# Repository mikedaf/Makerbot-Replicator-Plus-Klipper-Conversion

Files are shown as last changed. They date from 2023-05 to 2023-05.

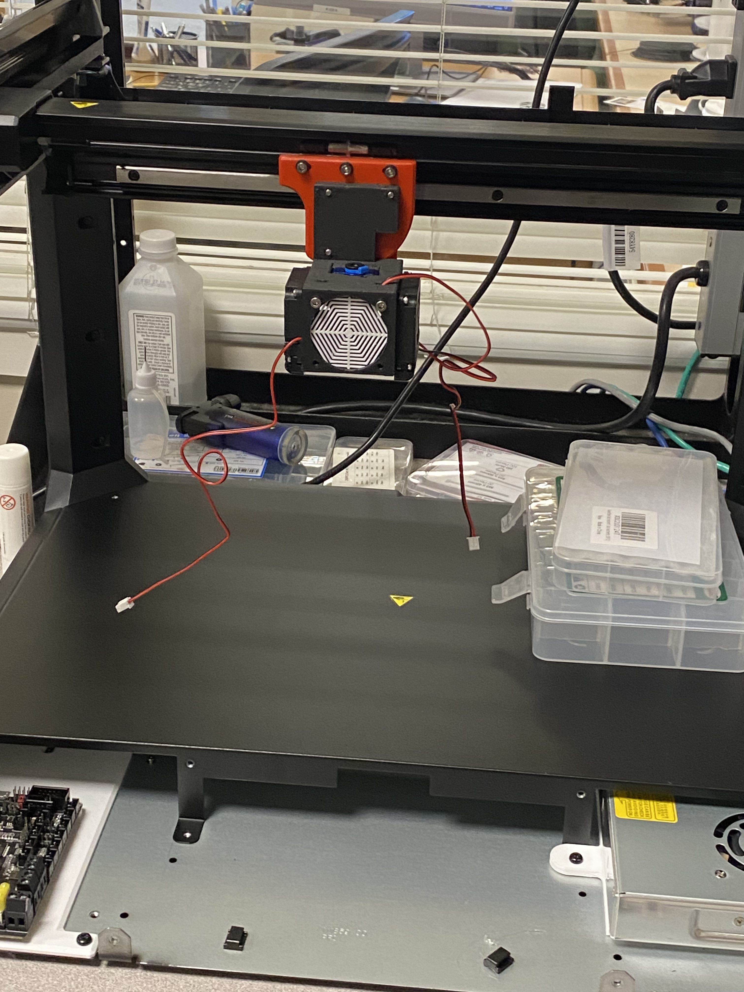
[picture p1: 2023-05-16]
Build Images/IMG_1790.jpg

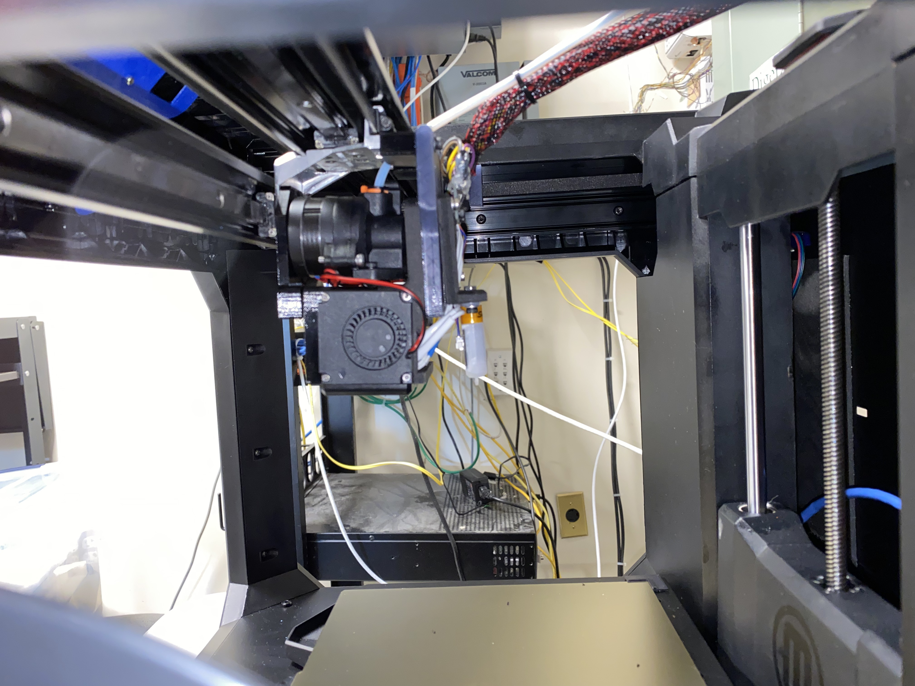
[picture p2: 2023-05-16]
Build Images/IMG_2500.jpg

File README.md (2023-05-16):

Here is everything I used to convert our Makerbot Replicator to a fairly capable klipper machine with a heated bed and input shaper.

I heavily used Rolohaun's makerbot replicator 5th gen parts for this, but I had to change some things for this specific printer. https://github.com/rolohaun/Replicator5-Klipper

This build uses M3 M2.5 and M2 screws, I used socket head ones, but any should be fine. Just be careful not to split the parts if you use countersunk screws. You'll need to source a good amount of M3 screws from M3x6 to M3x50. a regular M2.5 and M2 kit should cover those fine.

Some items may not work as intended, I've never done this before so let me know if something isn't working. The screen mount will probably not work as it is at the moment, but some post processing got it there for me.

I've included my toolhead STEP file, hopefully it can prove useful if anyone needs to make any changes.

I will comment out everything from the configs that won't run on an initial klipper setup, so make sure to uncomment these as you install ADXL support and so on.

I mounted the raspberry pi to where the old screen PCB and other bits were located. Use the original face plate piece and just replace the metal bracket with the printed one. You may have to cut some holes into the face plate sides to achieve enough room for the pi. I couldn't fit a power plug in there, so I soldered a ground wire to the usb housing chasis and stuck power across the two front GPIO pinsto save space. I hotglued the original encoder wheel back in place, but this is completely optional. The several usb,ethernet, and ADXL wires can be run along the top of the motion system where the original HMDI cord was set, there is enough room where they don't get pinched, but be careful because it's very easy for a wire to move into a location where it will get pinched. (Make sure to wire the original ground from the motion system frame into a common ground(also a good idea to do this with the PSU body))

The SKR Mini e3 v3 and Meanwell 350 PSU go in fairly simple, you'll need to have the entire machine apart for this, but you should already be there from taking the old parts out. Run the mainboard power wires around the same way the stock ones were run (under and in front of the Z platform). I cut a hole in the back panel and wired up a standard plug socket as well as an ethernet wall port and a plug for the Rpi power. this isn't difficult as theres plenty of room, but it can be a pain to get through that thick metal unless you have sufficient tools. The mainboard mount and the mainboard fan mount will sandwich the SKR mini together, but it can be easier to install the board on the mounting plate first with 1 or 2 of the thumbscrews, and then put the fans on with screws from the bottom. Make sure to only put the thumbscrews on the mounting point NOT used by the fan mounts.

The toolhead is a bit complex, it's probably easiest to assemble most of it outside the printer with the mainboard side wires disconnected. Use the dragonfly spacer and screw down the hotend (pretty much everything should use threaded inserts here). Now you can use the 4010 blower fans to hold the back and front hotend halves together (don't put any screws in the front top holes for the fan yet). Now is a good time to put the inserts for the LDO orbiter in place, and screw that down (the PTFE tube can be tricky to cut to length). Now screw the Toolhead mounting plate with 3 M3 screws along with the bltouch bracket to the back of the hotend assembly (the cables should be able to route through this part) You can then put the 4010 axial fan into the Front hotend part along with the fan grill and route the cable through one of the top holes (you'll need to cut the connector off if it has one).Next you'll go over to the metal plate that attaches the two rail carriages together on the printer, and just take out the 4 screws on the bottom vertical part. Then you'll mount the "Rail-Fan Mount" and screw that down. Then stick two M3x45-50 screws into the front two holes of that, followed by 3 washers on each one after they're pushed in. Now you can take the toolhead assembly and push it over the two long screws coming from the rail mount and it should hold everything in place. Don't full tighten this down yet, but instead put the Toolhead mounting spacer in place where it will screw into the original toolhead mounting holes (3 M3 holes). Now tighten everything in place and the toolhead should be good.

The cable guide just VHB tapes to the open rectangle shaped hole towards the back of the machine, this is covering the spot where the old spool holder was. That is completely useless to us now, so we'll cover it up with this. This can be added or removed after the hotend is already wired and tied up.

The side mounted spool holder is not my design, if I can find the original one I will link it in here, but there have been a couple options i've seen. I had to mirror this one so it would sit on the right side of the machine, but anything you can get to work will do the trick really.

The neopixels are completely optional, the wiring kinda sucks because the data needs to go directionally, while the power is best supplied directly. This machine has a lot of open space to mount these though, so get creative if you feel like it.

I did not set out to make this a cheap as can be upgrade, nor did I spend extra time making it easier than necessary. It should work as it is and it should be a reliable enough machine I would hope. (not much time on mine yet)

BOM:

SKR Mini e3 v3 (I just used this one because i've used it before and it's easy to setup for me)
https://www.amazon.com/BIGTREETECH-Control-TMC2209-Stepper-Upgrade/dp/B09LC34SCK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

Dragonfly BMS (you'll need to adjust some stuff to fit a different hotend)
https://www.amazon.com/Dragon-Printer-Compatible-Extruder-Creality/dp/B08MF9NPMT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

24v 60w Heater cartidge (interchangeable with any regular heater cartidge)
https://www.amazon.com/24V-60W-Temperature-Cartridge-Extruder/dp/B08CNCHC29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

Thermistor x2 (bed and hotend)
https://www.amazon.com/HT-NTC100K-Thermistor-Creality-Compatible-Ender-3-5/dp/B09WDR1M5Q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

4010 Axial fans x3
https://www.amazon.com/WINSINN-Ender-Upgrade-Bearing-CR-10S/dp/B08R9L9YR2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

4010 Blower fans x2
https://www.amazon.com/WINSINN-Blower-Upgrade-Bearing-CR-10S/dp/B08R9J189W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

BLTouch Probe (feel free to fit a limit switch to this somehow)
https://www.amazon.com/Creality-Upgraded-BLTouch-Leveling-Mainboard/dp/B08MD3ZJTD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

Meanwell LRS 350 (I chose this because I know it can handle everything it needs to, and I like to go with reputible PSUs)
https://www.amazon.com/MEAN-WELL-LRS-350-24-Switching-Printer/dp/B07SQLJG5L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

Power socket and switch
https://www.amazon.com/FILSHU-Socket-Module-Wiringiec320-illuminated/dp/B08L2522DF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

Ethernet Ports x1
https://www.amazon.com/VICTEK-Female-Keystone-Couplers-White/dp/B01JJ46JX4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

PET Expandable cable sleeving
https://www.amazon.com/PET-Expandable-Sleeving-PureBlack-BlackRed/dp/B081MRG8BT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

USB A to female USB A Cable (can be used to connect pi to mainboard)
https://www.amazon.com/Sabrent-22AWG-Extension-Cable-Female/dp/B019DZG9DY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

Silicone heater pad 200x150 24v (will need to tape on thermistor)
https://www.aliexpress.us/item/2255800268049970.html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 200x150 24v

Die Springs 18x20mm x3 (used for bed)
https://www.amazon.com/uxcell-Printer-Stamping-Compression-Electric/dp/B0BVKDT67R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 18x20mm x4

M6 Screw assortment (M6x25-30 should work, but untested (used for bed))
https://www.amazon.com/Cicidorai-Stainless-Assortment-Machine-Threads/dp/B08Z7BW2XG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

Springsteel PEI buildplate 200x300mm
https://www.aliexpress.us/item/2255800124796619.html?gatewayAdapt=glo2usa4itemAdapt&_randl_shipto=US 200x300mm

LDO Orbiter extruder
https://www.printedsolid.com/products/ldo-orbiter-v2-dual-drive-direct-extruder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

Heatshrink solder connectors (completely optional)
https://www.amazon.com/Connectors-Sopoby-Waterproof-Electrical-Automotive/dp/B0BKSJQC9Q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

Stepper Motors x2 (optional)
https://www.amazon.com/STEPPERONLINE-Stepper-63-74oz-Connector-Extruder/dp/B07LCK19D5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

PiTFT43
https://www.amazon.com/BIGTREETECH-Raspberry-Controller-Capacitive-105-5X67mm/dp/B09791ZG1B

RPi Ribibon cables
https://www.amazon.com/Arducam-Raspberry-Camera-Ribbon-Extension/dp/B07SM6JTTM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

PTFE Tubing
https://www.amazon.com/Teflon-tubing-Filament-Printer-Tech/dp/B073RDFTDV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

Heatset Inserts
https://www.amazon.com/EEEEE-Threaded-Assortment-Printing-Injection/dp/B0B47MZ1SG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

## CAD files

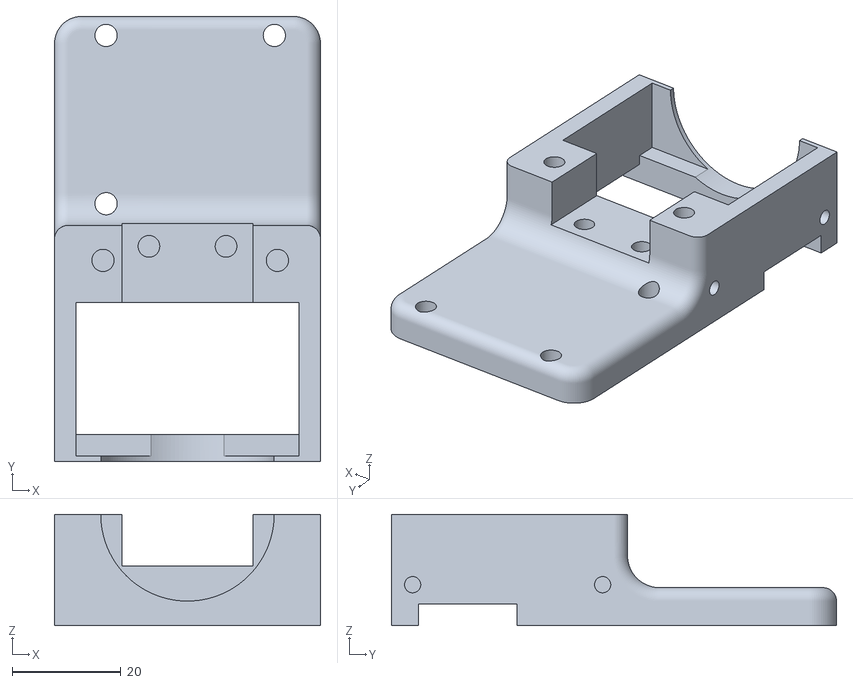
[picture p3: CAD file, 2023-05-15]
STLs/Toolhead/Hotend mainbody.stl
49.0 x 82.0 x 20.5

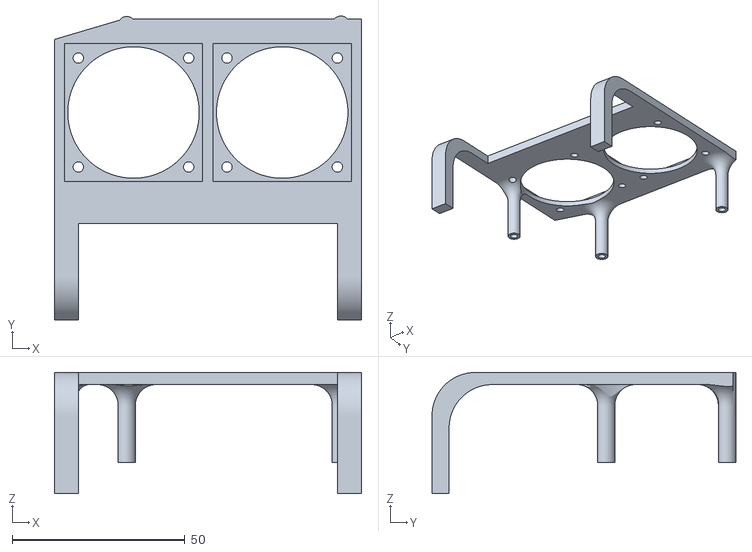
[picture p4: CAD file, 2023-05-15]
STLs/backside-electronics/SKR board fans mount.stl
88.9 x 87.9 x 35.0

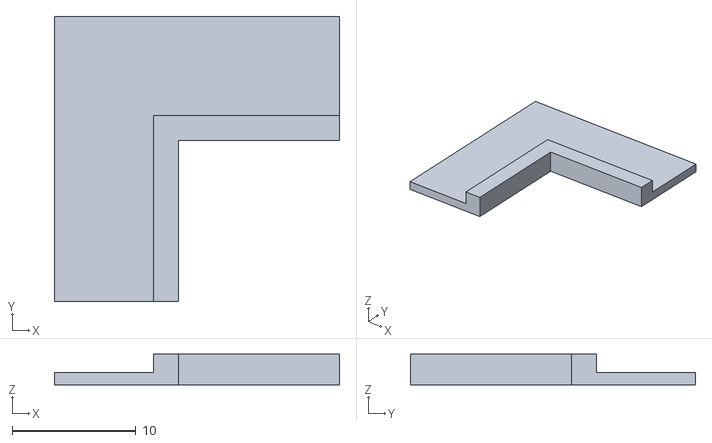
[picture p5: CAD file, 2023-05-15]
STLs/Bed/PEI bedsheet alignment guide x2.stl
23.0 x 23.0 x 2.50

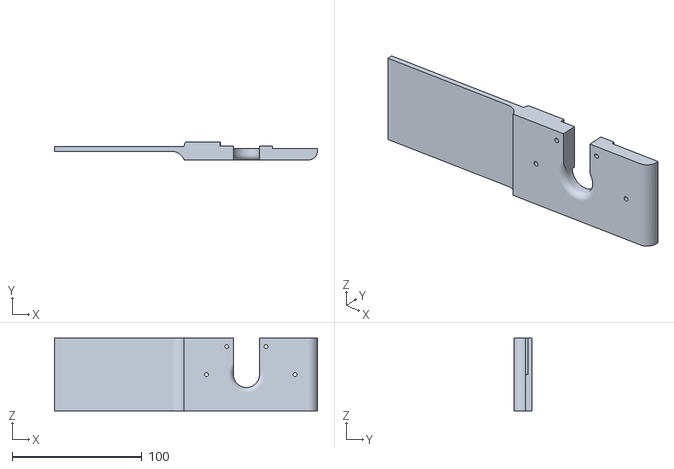
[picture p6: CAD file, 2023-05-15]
STLs/Cable Guide/Hotend wire loom guide pt1.stl
202.6 x 13.6 x 55.9

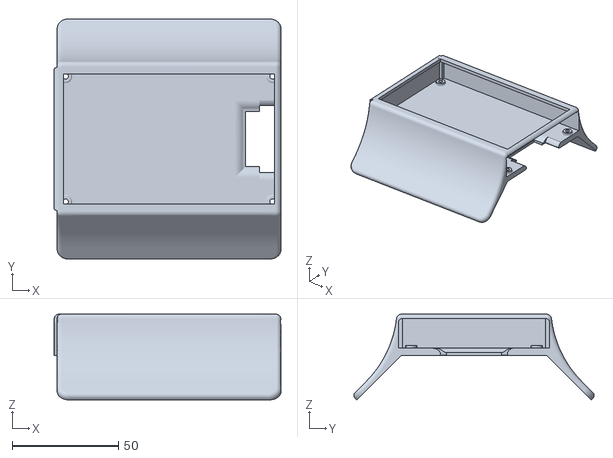
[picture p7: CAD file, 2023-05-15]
STLs/Raspberry Pi and Screen/PiTFT43 Mount (WIP).stl
107.0 x 113.2 x 40.5

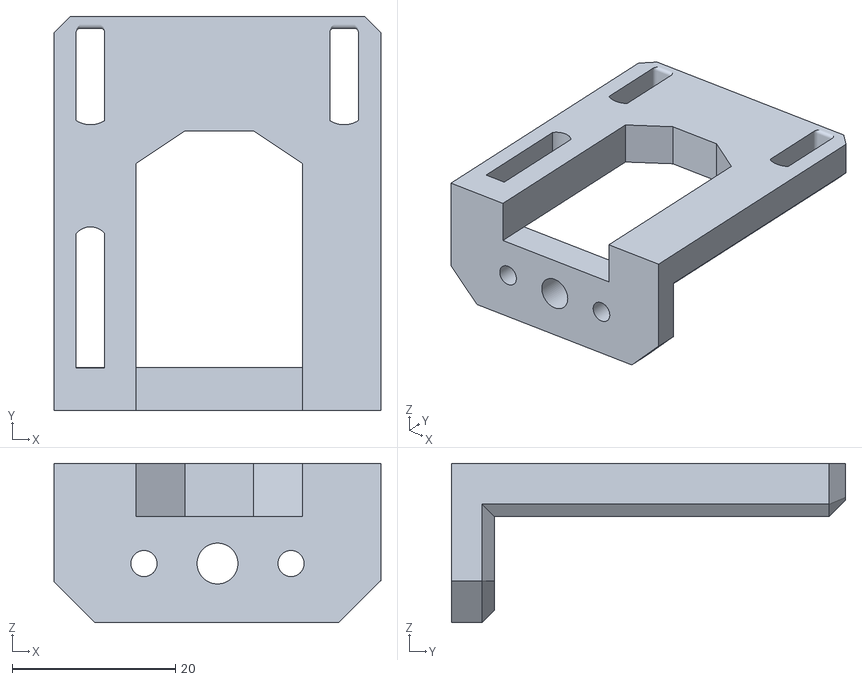
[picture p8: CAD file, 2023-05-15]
STLs/Toolhead/BLTouch mount.stl
40.0 x 48.2 x 19.5

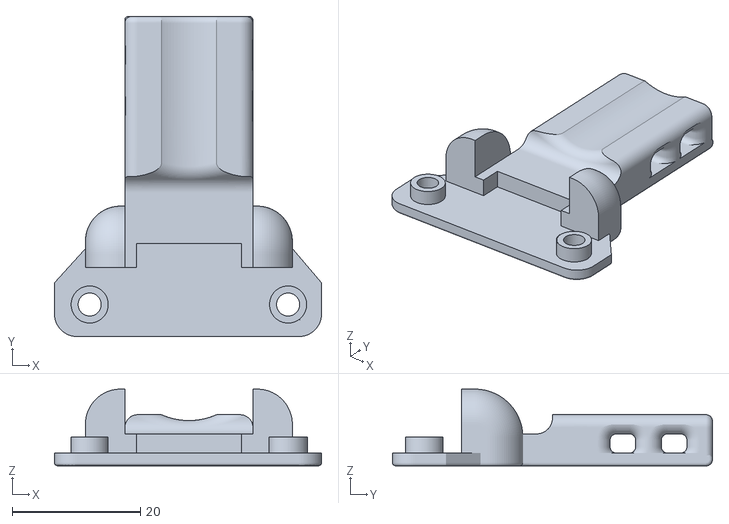
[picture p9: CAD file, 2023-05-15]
STLs/backside-electronics/Nema 17 wire strain relief x2.stl
41.7 x 50.0 x 12.0

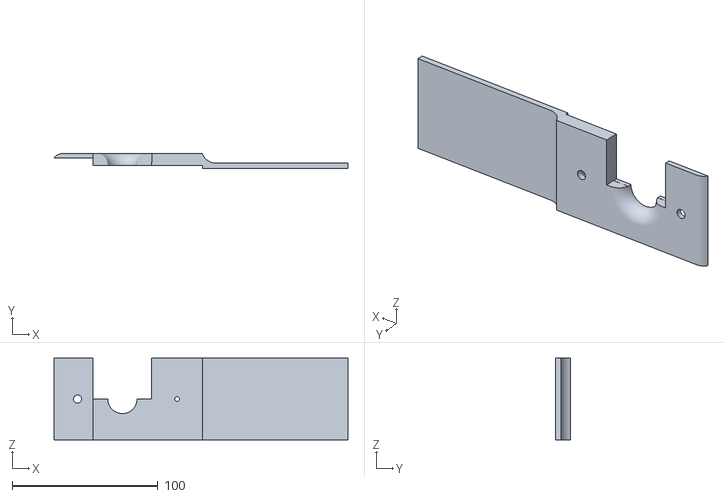
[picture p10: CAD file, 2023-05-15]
STLs/Cable Guide/Hotend wire loom guide pt2.stl
201.4 x 10.1 x 55.9

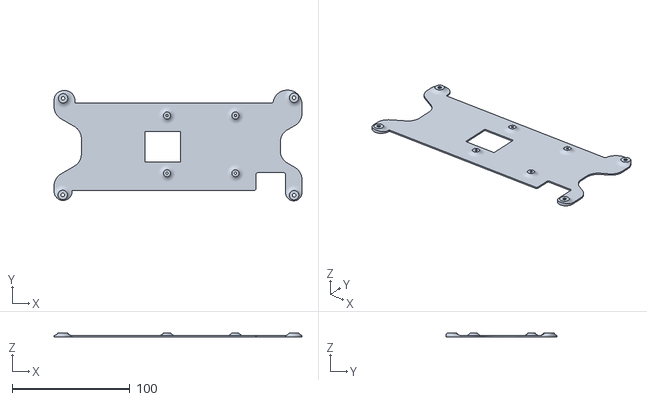
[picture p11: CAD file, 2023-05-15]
STLs/Raspberry Pi and Screen/Rpi mounting bracket.stl
210.4 x 93.9 x 3.75

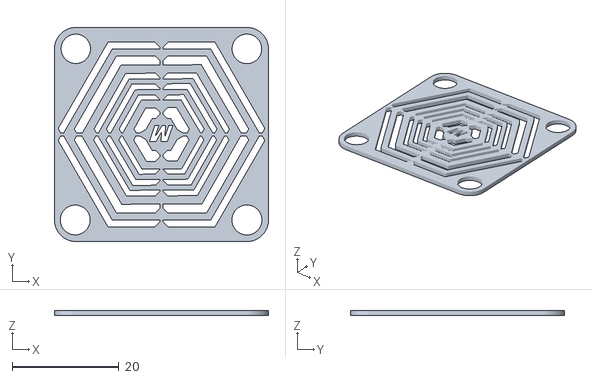
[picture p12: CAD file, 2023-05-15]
STLs/Toolhead/40mm Fan Grill.stl
40.0 x 40.0 x 1.00

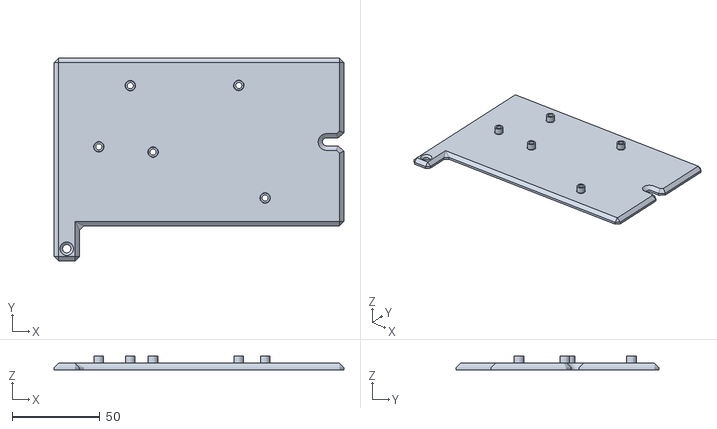
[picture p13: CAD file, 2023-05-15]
STLs/backside-electronics/SKR Mini e3 v3 mount.stl
165.5 x 115.7 x 8.20

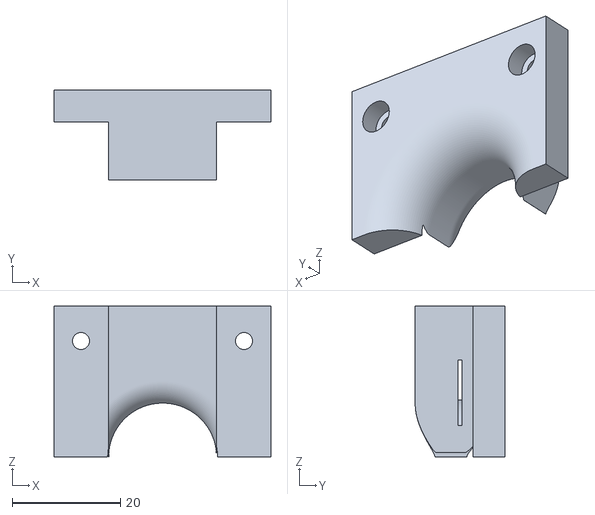
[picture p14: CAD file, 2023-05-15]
STLs/Cable Guide/Hotend wire loom guide pt3.stl
40.2 x 16.6 x 27.9

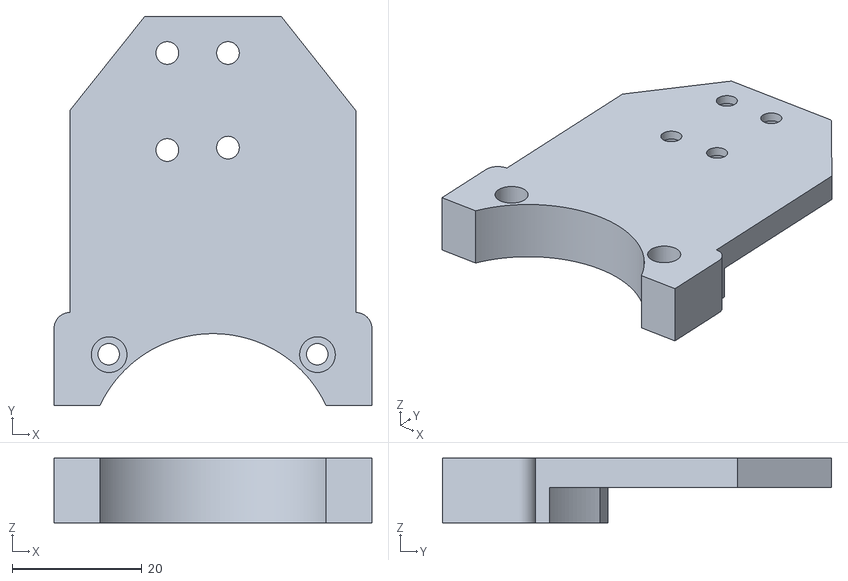
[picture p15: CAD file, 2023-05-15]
STLs/Toolhead/Rail-Fan mount.stl
49.0 x 60.0 x 10.0

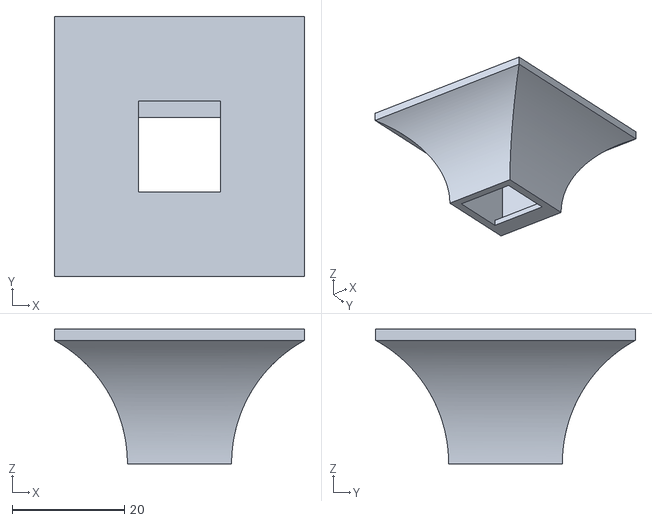
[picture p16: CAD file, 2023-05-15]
STLs/backside-electronics/Ethernet wall jack Inside mount.stl
44.6 x 46.3 x 24.0

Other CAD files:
STLs/Toolhead/Dragonfly BMS spacer.stl
STLs/Toolhead/Toolhead mounting spacer.stl
STLs/backside-electronics/Ethernet wall jack Outside mount.stl
STLs/backside-electronics/Meanwell 350 mount.stl
STLs/Toolhead/Hotend Front body.stl
STLs/Toolhead/Toolhead mounting plate.stl
STLs/backside-electronics/M3 Thumbscrew x1-3.stl

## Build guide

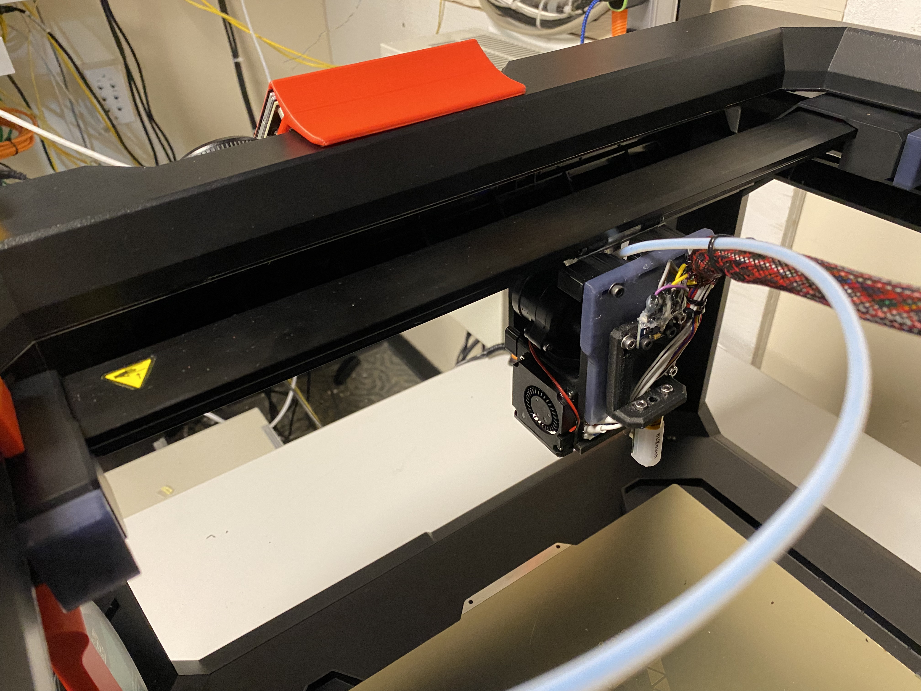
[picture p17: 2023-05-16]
Build Images/IMG_2492.jpg

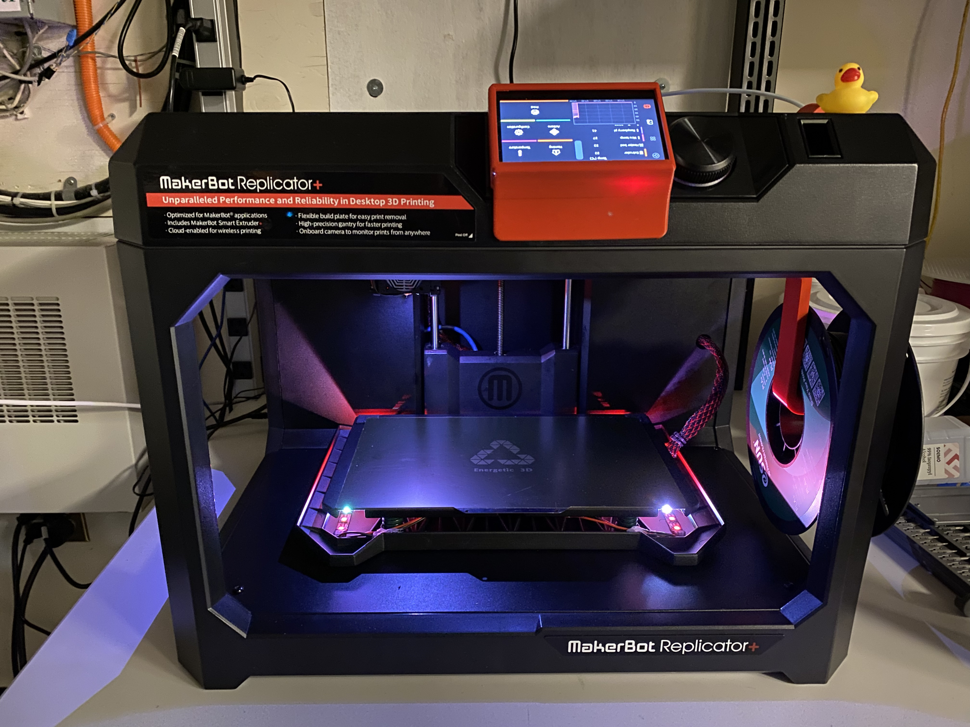
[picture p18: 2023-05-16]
Build Images/IMG_2513.jpg

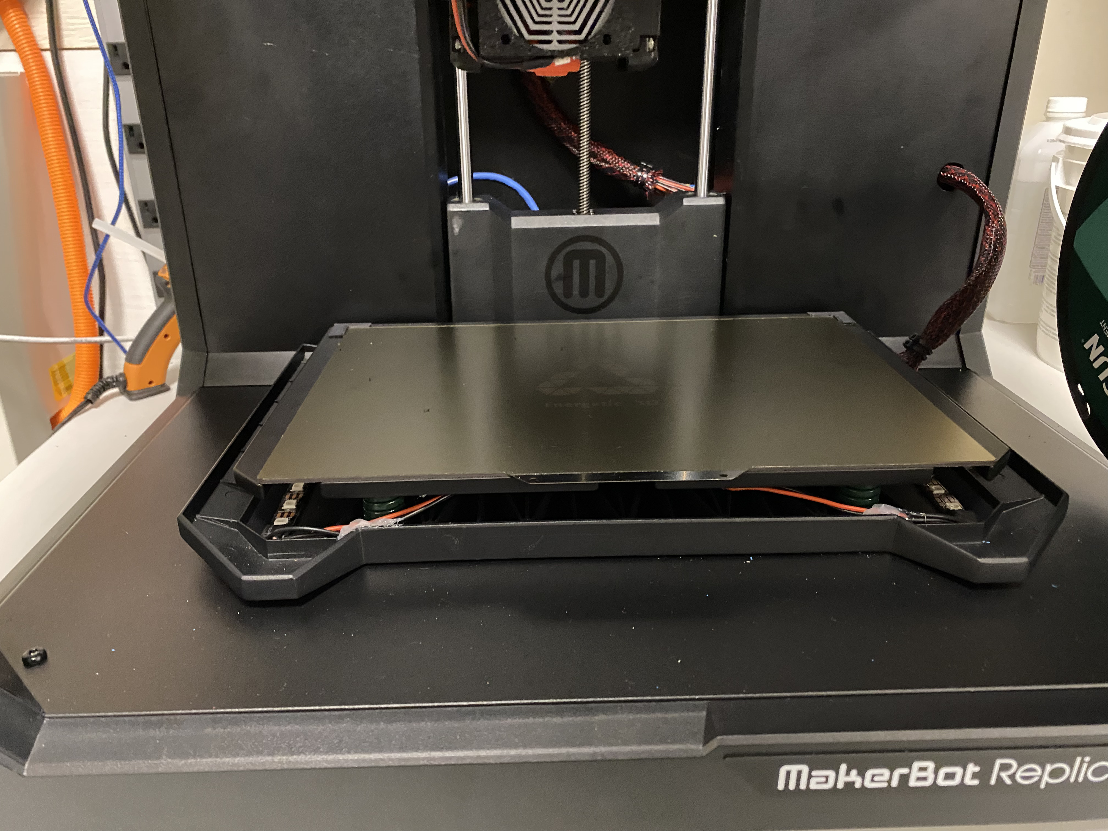
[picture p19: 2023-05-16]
Build Images/IMG_2494.jpg

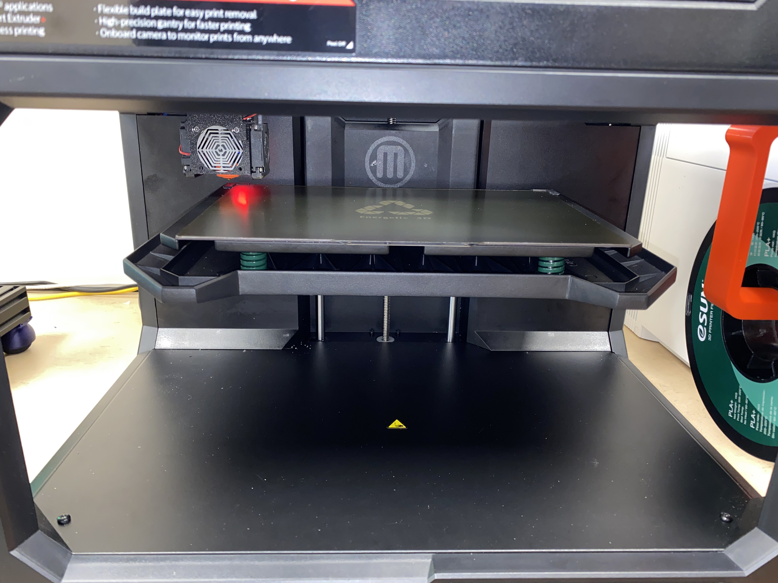
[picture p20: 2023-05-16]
Build Images/IMG_2347.jpg

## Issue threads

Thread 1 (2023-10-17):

Wiring

jamsbach, 2023-10-17:
Hello, I am partway through completing my own conversion with Mainsail working and most of the wires ready. I was wondering if you would be able to send an image of your wiring specifically of the motors.

mikedaf, 2024-01-27:
I'm sorry I meant to reply to this a long time ago, but I never sent it apparently.
If you still need pictures of anything I can post some when I get back to work on Monday. _

jamsbach, 2024-01-27:
No, I have permanently put the project on hold.

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

mikedaf, 2024-01-27:
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

Sorry to hear that, if you ever want to continue don't hesitate to ask anything.

Closed 2025-10-01.

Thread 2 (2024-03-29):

Video information?

mp3llll, 2024-03-29:
How are you?
Do you have any video information how to make all think work?

mikedaf, 2024-03-29:
Hello, I'm doing good, thank you
What do you mean video information? Like a video of it printing? I should have uploaded photos of the internals if I remember correctly.

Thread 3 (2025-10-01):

Bed Wiring

CoreXYForge, 2025-10-01:
Could you provide more information on how you attached the bed heater/flex plate? I am converting one right now using an SKR pico. I know how to wire everything, but there isn't any information on how to attach the bed.

CoreXYForge, 2025-10-02:
I almost convinced myself to put a stealthburner on it lol. In my opinion, this machine was wasted potential. Makerbot could have mounted multiple of the magnetic quick swap "smart" extruders on the back panel, and added some gcode to make it a toolchanger. That would have been really simple to implement and it may have made the machine worth using.

Closed 2025-10-01.

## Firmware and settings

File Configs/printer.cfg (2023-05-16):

#Klipper Config for Not-A-Makerbot
  #SKR Mini e3 V3
  #LDO Orbiter v2
  #H-Bot Corexy
  #BLTouch
  #Sensorless homing
  #Screw Calculate
  #Auto Leveling
  #PID Autotune
#Compiled 5-14-23

[printer]
kinematics: corexy
max_velocity: 100
max_accel: 2300
max_z_velocity: 50
max_z_accel: 100

[mcu]
serial: /dev/serial/by-id/usb-Klipper_stm32g0b1xx_4F00410002504B5735313920-if00 # restart_method: command

#[mcu rpi]
#serial: /tmp/klipper_host_mcu

[heater_fan heatbreak_cooling_fan]
pin: PC7

[heater_fan controller_fan]
pin: PB15

[fan]
pin: PC6

[virtual_sdcard]
path: /home/pi/printer_data/gcodes
on_error_gcode: CANCEL_PRINT

[delayed_gcode sd_card_auto_init]
initial_duration: 5
gcode:
  M21
  M20  

[display_status]

[pause_resume]

[static_digital_output usb_pullup_enable]
pins: !PA14

[board_pins]
aliases:
    # EXP1 header
    EXP1_1=PB5,  EXP1_3=PA9,   EXP1_5=PA10, EXP1_7=PB8,  EXP1_9=<GND>,
    EXP1_2=PA15, EXP1_4=<RST>, EXP1_6=PB9,  EXP1_8=PB15, EXP1_10=<5V>

# Enable arcs support
[gcode_arcs]
resolution: 0.1

# Enable object exclusion
[exclude_object]

[include BLTouch.cfg]
[include Extruder.cfg]
[include X_Axis.cfg]
[include Y_Axis.cfg]
[include Z_Axis.cfg]
[include Bed.cfg]
[include Start.cfg]
[include End.cfg]
[include Pause.cfg]
[include Resume.cfg]
[include Cancel.cfg]
[include PID.cfg]
#[include ADXL345.cfg]
[include Filament.cfg]
[include BedLevel.cfg]
[include HomeCheck.cfg]
[include NozzleMid.cfg]
[include Temps.cfg]
#[include Neopixel.cfg]
#[include ExcludeObj.cfg]

#*# <---------------------- SAVE_CONFIG ---------------------->
#*# DO NOT EDIT THIS BLOCK OR BELOW. The contents are auto-generated.
#*#
#*# [extruder]
#*# control = pid
#*# pid_kp = 20.103
#*# pid_ki = 1.090
#*# pid_kd = 92.727
#*#
#*# [heater_bed]
#*# control = pid
#*# pid_kp = 47.406
#*# pid_ki = 1.663
#*# pid_kd = 337.768
#*#
#*# [bltouch]
#*# z_offset = 3.604
#*#
#*# [bed_mesh default]
#*# version = 1
#*# points =
#*# 	  0.000000, -0.002500, -0.002500, 0.036250, 0.066250, 0.107500, 0.125000, 0.166250, 0.130000, 0.083750, 0.032500, 0.022500, 0.025000, 0.018750, 0.016250
#*# 	  -0.091250, -0.061250, -0.011250, 0.035000, 0.066250, 0.100000, 0.101250, 0.113750, 0.102500, 0.093750, 0.061250, 0.067500, 0.048750, 0.016250, -0.018750
#*# 	  -0.131250, -0.053750, 0.046250, 0.097500, 0.122500, 0.158750, 0.172500, 0.157500, 0.151250, 0.168750, 0.136250, 0.128750, 0.115000, 0.053750, -0.012500
#*# 	  -0.108750, -0.023750, 0.080000, 0.136250, 0.163750, 0.203750, 0.205000, 0.163750, 0.192500, 0.206250, 0.167500, 0.160000, 0.147500, 0.082500, 0.008750
#*# 	  -0.061250, 0.011250, 0.078750, 0.133750, 0.175000, 0.207500, 0.177500, 0.147500, 0.171250, 0.201250, 0.172500, 0.160000, 0.146250, 0.095000, 0.038750
#*# 	  -0.025000, 0.020000, 0.061250, 0.112500, 0.167500, 0.202500, 0.187500, 0.195000, 0.198750, 0.180000, 0.146250, 0.145000, 0.136250, 0.082500, 0.043750
#*# 	  -0.067500, -0.028750, 0.032500, 0.108750, 0.165000, 0.205000, 0.218750, 0.223750, 0.202500, 0.182500, 0.165000, 0.166250, 0.136250, 0.067500, 0.016250
#*# 	  -0.082500, -0.045000, 0.023750, 0.095000, 0.147500, 0.195000, 0.207500, 0.207500, 0.188750, 0.166250, 0.161250, 0.143750, 0.100000, 0.046250, -0.001250
#*# 	  -0.093750, -0.026250, 0.023750, 0.038750, 0.098750, 0.171250, 0.177500, 0.166250, 0.163750, 0.175000, 0.135000, 0.096250, 0.070000, 0.052500, 0.005000
#*# 	  -0.122500, -0.052500, -0.037500, -0.037500, 0.042500, 0.127500, 0.107500, 0.081250, 0.093750, 0.130000, 0.083750, 0.023750, 0.001250, 0.015000, -0.026250
#*# 	  -0.151250, -0.092500, -0.096250, -0.093750, -0.012500, 0.077500, 0.036250, 0.008750, 0.035000, 0.093750, 0.047500, -0.021250, -0.035000, -0.028750, -0.051250
#*# x_count = 15
#*# y_count = 11
#*# mesh_x_pps = 2
#*# mesh_y_pps = 2
#*# algo = bicubic
#*# tension = 0.2
#*# min_x = 5.0
#*# max_x = 289.9
#*# min_y = 17.0
#*# max_y = 189.0

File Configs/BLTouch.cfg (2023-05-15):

[bltouch]
sensor_pin: ^PC14
control_pin: PA1
x_offset: 2
y_offset: 42
#z_offset: 0
probe_with_touch_mode: true
stow_on_each_sample: false
pin_move_time: 0.5
pin_up_touch_mode_reports_triggered: False
speed: 10
lift_speed: 30
samples: 2
sample_retract_dist: 2.5
samples_tolerance_retries: 3

[safe_z_home]
home_xy_position: 144,67.5
speed: 100
z_hop: 10
z_hop_speed: 20
move_to_previous: true

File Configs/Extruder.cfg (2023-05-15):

[extruder]
step_pin: PB3
dir_pin: PB4
enable_pin: !PD1
microsteps: 16
full_steps_per_rotation: 200
rotation_distance: 4.637
nozzle_diameter: 0.400
filament_diameter: 1.750
heater_pin: PC8
sensor_type: Trianglelab NTC100K B3950
sensor_pin: PA0
#control: pid
#pid_Kp: 18.915
#pid_Ki: 0.993
#pid_Kd: 90.085
min_temp: -100
max_temp: 300
max_extrude_only_distance: 500.0
max_extrude_only_velocity: 120
max_extrude_only_accel: 6400
pressure_advance: 0.0552
pressure_advance_smooth_time: 0.03

[thermistor Trianglelab NTC100K B3950]
## values calibrated against a PT100 reference
temperature1: 25.0
resistance1: 103180.0
temperature2: 150.0
resistance2: 1366.2
temperature3: 250.0
resistance3: 168.6

[tmc2209 extruder]
uart_pin: PC11
tx_pin: PC10
uart_address: 3
run_current: 0.85
hold_current: 0.1
stealthchop_threshold: 999999

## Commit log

2023-05-15 Added Config files
    [ADXL345 (1).cfg, BLTouch.cfg, Bed.cfg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]
2023-05-15 Included STL files
    [40mm Fan Grill.stl, BLTouch mount.stl, Dragonfly BMS spacer.stl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]
2023-05-16 Configs ready for fresh klipper install
    I commented out the Rpi mcu, the ADXL.cfg and the neopixel.cfg. These can be installed and uncommented after initial setup.
    [ADXL345.cfg, BedLevel.cfg, ExcludeObj.cfg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]
